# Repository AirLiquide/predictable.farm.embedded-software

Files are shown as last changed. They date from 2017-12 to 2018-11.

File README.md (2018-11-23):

Predictable Farm — Embedded software
---

### Introduction

Two versions are available :

  - a legacy version for the **Arduino Yùn** (_it was the first platform used for the predictable.farm project_)
  - An up-to-date version for the **Siemens IOT2000** boards

### Licenses

Our work is licensed under the MIT license. See license.txt.

**This work uses sofware that is licensed under CC BY-NC-SA 3.0, GNU LGPL, and BSD licenses. The respective files have kept their original license notices.**

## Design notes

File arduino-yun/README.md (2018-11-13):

Predictable Farm — Embedded software — Yùn Bridge Flavour
---

### Introduction

This folder contains the code for the Yùn version, including :

  - `arduino-IO-node` : the code for the ATmega32u4 microcontroller;
  - `linino` : the code for the Linino Linux distribution running on the Atheros chipset.

See the relevant README in each folder for more information.

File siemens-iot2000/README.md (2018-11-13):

Predictable Farm — Embedded software — Siemens iot2000 flavour
---

### Introduction

This is the on-board software for the predictable farm devices.
It is self-updateable via [SWUpdate](https://github.com/sbabic/swupdate).

**Configuration**

The zone pattern indicate the naming pattern for the farms, e.g. `http://farm1.my.domain`, `http://farm2.my.domain`, if necessary. Else, the default server url is used.

Devices are supposed to be hostnamed as per the following pattern : `predictable{XXX}.local` where `{XXX}` is an integer.

### Installation

Dependencies : **mraa** and **socket.io**

> This software is to be installed on the device; hence, having limited resources, we favor a general installation of dependencies, not using `npm`.
> As such, node modules should be installed in `/usr/lib/node_modules/` beforehand; We do not provide a `package.json` file for this repo (but it would be trivial to do so if you need it).

The `start.sh`  script should be launched at boot time.

The `local-engine.js` file is the compiled bundle from the [Predictable farm offline strategy generator](http://airliquide.github.com/predictable.farm.embedded-software.offline-strategy-generator). If the latter is updated, compile it for `iot2000` and put it in the root folder of your installation.

### To start everything

    cd predictable-farm
    forever start forever.json

### To stop all services 

    forever stopall

### To operate on a single script

    forever restart <script>

### Relevant documentation

  - [Intel IOT MRAA lib](http://iotdk.intel.com/docs/master/mraa/node/classes/i2c.html#method_readWordReg)
  - [MRAA Galileo Gen 2 limitations](https://github.com/intel-iot-devkit/mraa/blob/master/docs/galileorevh.md)
  - [Galileo Gen 2 Pin mapping](https://link.springer.com/chapter/10.1007/978-1-4302-6838-3_14)
  - [Quark X1000 i2C documentation](https://github.com/slavaim/Linux-Intel-Galileo-Gen2-QuarkX1000/tree/master/BSPv1.1.0/linux_v3.8.7/work/Documentation/i2c)

### To enable / disable the i2c bus power

    mraa-gpio set 04 00 # Disable
    mraa-gpio set 04 01 # Enable

### To force-stop the i2c bus

    # Force deactivate PIN gpio6 (IO4) - Bus I2C
    echo 0 > /sys/class/gpio/gpio6/value

### To create a new release / update the code

We use SWupdate (https://github.com/sbabic/swupdate) with its Yocto layer : https://github.com/sbabic/meta-swupdate/tree/morty.

    ./create_release.sh

This will create a `predictable-farm_<version>.swu` file in the root folder, that can be used with swupdate on the target device :

    swupdate_unstripped --hwrevision iot2040:rev1 -i predictable-farm_<version>.swu

> release_install.sh and release_restart.sh are pre and post install scripts used by swupdate during the update process.

### CAD Files

In order to build the necessary interface board, the CAD folder includes : the Fritzing source design + the BOM and relevant datasheets.

### License

MIT. See License.txt file

**This work uses sofware that is licensed under GPL-2.0. The respective files have kept their original license notices.**

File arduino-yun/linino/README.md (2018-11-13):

Predictable Farm — Embedded software — Yùn Bridge Flavour
---

Needs NodeJS 0.10.* and BusyBox.

### Installation

Dependencies : **serialport** and **socket.io-client**

> This software is to be installed on the device; hence, having limited resources, we favor a general installation of dependencies, not using `npm`.
> As such, node modules should be installed in `/usr/lib/node_modules/` beforehand; We do not provide a `package.json` file for this repo (but it would be trivial to do so if you need it).

#### ID bootstrapping

To include the correct id, you must run the `scripts/bootstrap.sh` script first, with the correct ID in the **valueID** file.

#### How to install the bridge service

Node modules should be installed in `/usr/lib/node_modules/` beforehand; NPM is not a valid choice to install dependencies on this system.

copy `bridge.service` to `/etc/init.d/bridge` and make it executable :

    cp /root/bridge.service /etc/init.d/bridge
    chmod +x /etc/init.d/bridge

Enable it for auto starting at boot :

    /etc/init.d/bridge enable

#### Swap

It's better to have some swap to manage RAM overflows :

    cd /
    mkdir swap
    dd if=/dev/zero of=/swap/yunswapfile bs=1M count=512
    # wait a bit here, takes ~10min
    mkswap /swap/yunswapfile
    swapon /swap/yunswapfile
    uci add fstab swap
    uci set fstab.@swap[0].device=/swap/yunswapfile
    uci set fstab.@swap[0].enabled=1
    uci set fstab.@swap[0].fstype=swap
    uci set fstab.@swap[0].options=default
    uci set fstab.@swap[0].enabled_fsck=0
    uci commit # might trigger some errors, but that's ok
    reboot

#### Crontab

Make the reboot script executable if necessary :

    chmod +x /root/scripts/safeRebootAtMidnight.sh

And create a **crontab** for root :

    5 0 * * * /root/scripts/safeRebootAtMidnight.sh

#### Update code

Use the update script :

    /scripts/update.sh

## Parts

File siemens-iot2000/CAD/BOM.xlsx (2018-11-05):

Repère | Qté | Ref. Fabricant | Description | Fabricant | Fournisseur | Ref. Fournisseur | Prix unitaire | Prix total
J1 | 1 | EM366002 | Terminal bornier 2P 5mm | Bussman | Mouser | 504-EM366002 | 0.47 € | 0.47 €
J2 | 1 | S3B-PH-K-S (LF)(SN) | Connecteur 3 pin JST PH | JST | Digikey (ou RS) | 455-1720-ND | 0.15 | 0.15 €
J101, J102, 103, J104, 105, 106 | 6 | 110990030 | Connecteurs Grove | Seeed Studio | Mouser | 713-110990030 | 1.23 € | 1.23 €
U1 | 1 | 95503-2881 | Connecteur Ethernet RJ45 | Molex | Mouser | 538-95503-2881 | 0.69 € | 0.69 €
IC1, IC2 | 2 | FDS8958A-F085 | Dual N & P-Channel PowerTrench | Fairchild | Mouser | 512-FDS8958A | 0.76 € | 1.53 €
IC3 | 1 | TSR2-2450 | Convertisseur DC/DC | Traco | Mouser | 495-TSR2-2450 | 11.21 € | 11.21 €
D2,D3 | 2 | SMAJ60A-TP | Suppresseur ESD / diodes | MCC | Mouser | 833-SMAJ60A-TP | 0.51 € | 1.02 €
R7, R9 | 2 | MBB02070C1004FCT00 | 1 M 5% | Vishay | Mouser | 594-MBB02070C1004FCT | 0.08 € | 0.16 €
R8, R10 | 2 | MBB02070C4703FCT00 | 470k 1% | Vishay | Mouser | 594-MBB02070C4703FCT | 0.09 € | 0.19 €
R3, R4, R11, R12 | 4 | MBB02070C1002FCT00 | 10k 1% | Vishay | Mouser | 594-MBB02070C1002FCT | 0.09 € | 0.38 €
C1, C3 | 2 | K101J15C0GH53H5H | 100V, 0.1 nF (100pf) | Vishay | Mouser | 594-K101J15C0GH53H5H | 0.21 € | 0.43 €
C2, C4 | 2 | C315C102J3H5TA91707301 | 25V 1 nF | Kemet | Mouser | 80-C315C102J3H9170TR | 0.63 € | 1.26 €
C5 | 1 | C315C103M5U5TA | 50V 0.01µF | Kemet | Mouser | 80-C315C103M5U | 0.25 € | 0.25 €
Headers 20P - to break away | 2 | 22-28-4205 | Header breakaway 20P 1R | Molex | Mouser | 538-22-28-4205 | 0.92 € | 1.84 €
IC5 | 1 | TCA9517 | Level-Shifting I2C Bus Repeater | TI | Mouser | 595-TCA9517DR | 0.80 € | 0.80 €
 |  |  |  |  |  |  | Mouser | 21.44 €
 |  |  |  |  |  |  | Digikey | 0.15 €
 |  |  |  |  |  |  | Total | 21.59 €

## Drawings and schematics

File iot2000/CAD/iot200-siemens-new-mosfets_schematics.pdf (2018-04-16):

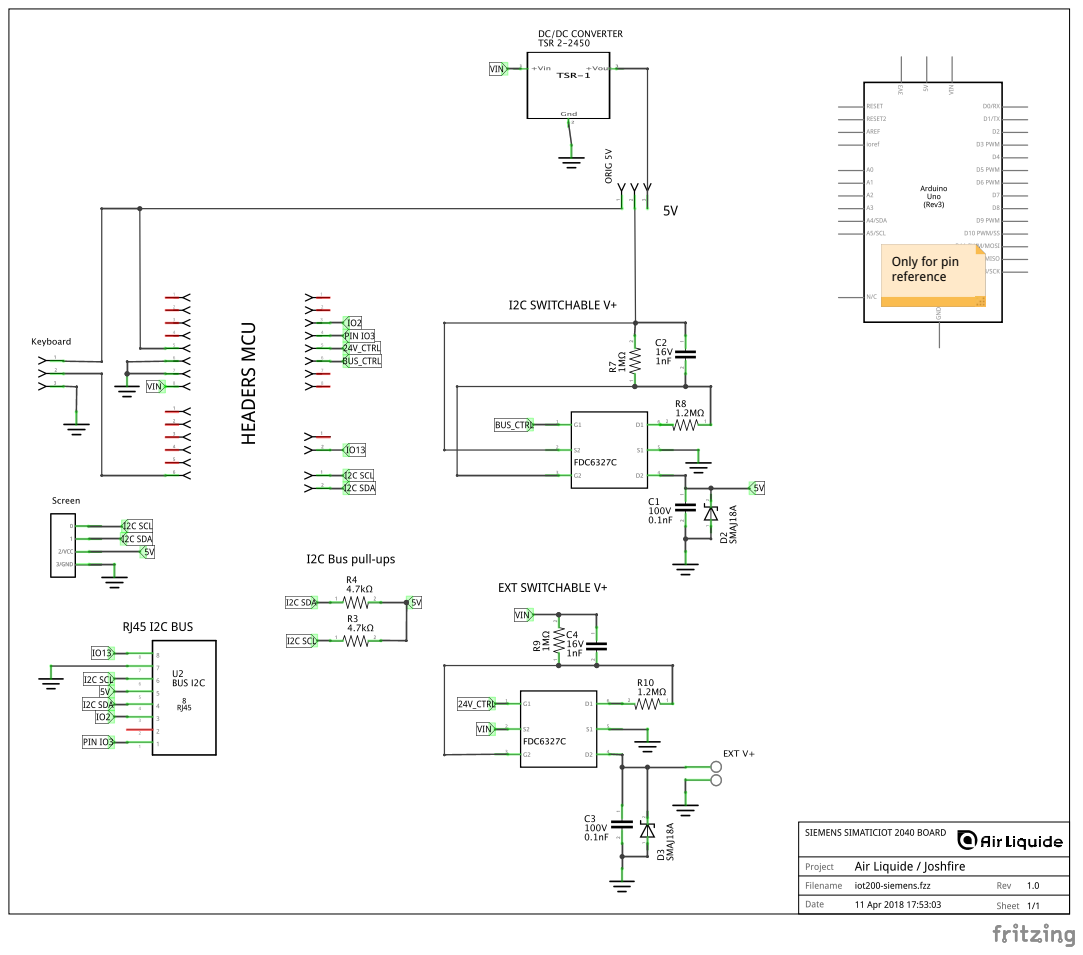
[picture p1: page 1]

Only for pin
reference

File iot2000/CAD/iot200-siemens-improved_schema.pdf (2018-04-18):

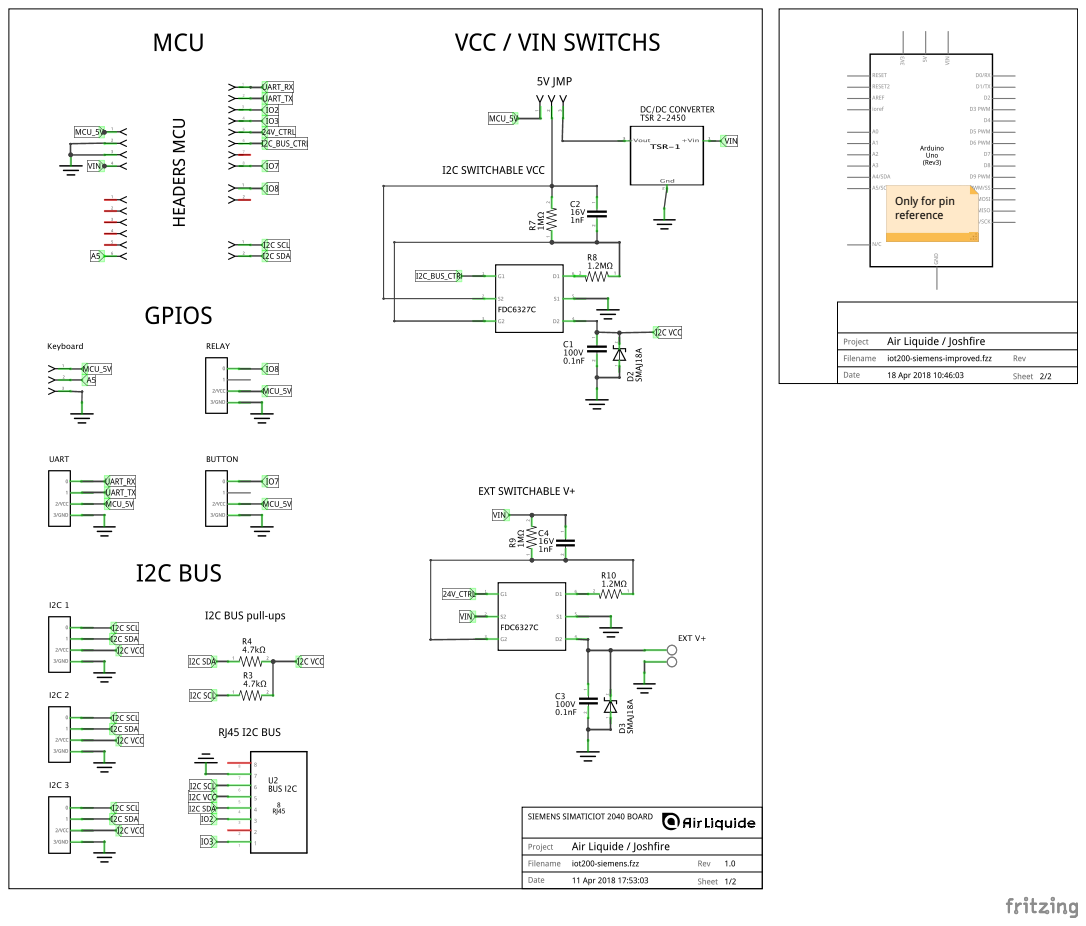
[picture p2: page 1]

Only for pin
reference

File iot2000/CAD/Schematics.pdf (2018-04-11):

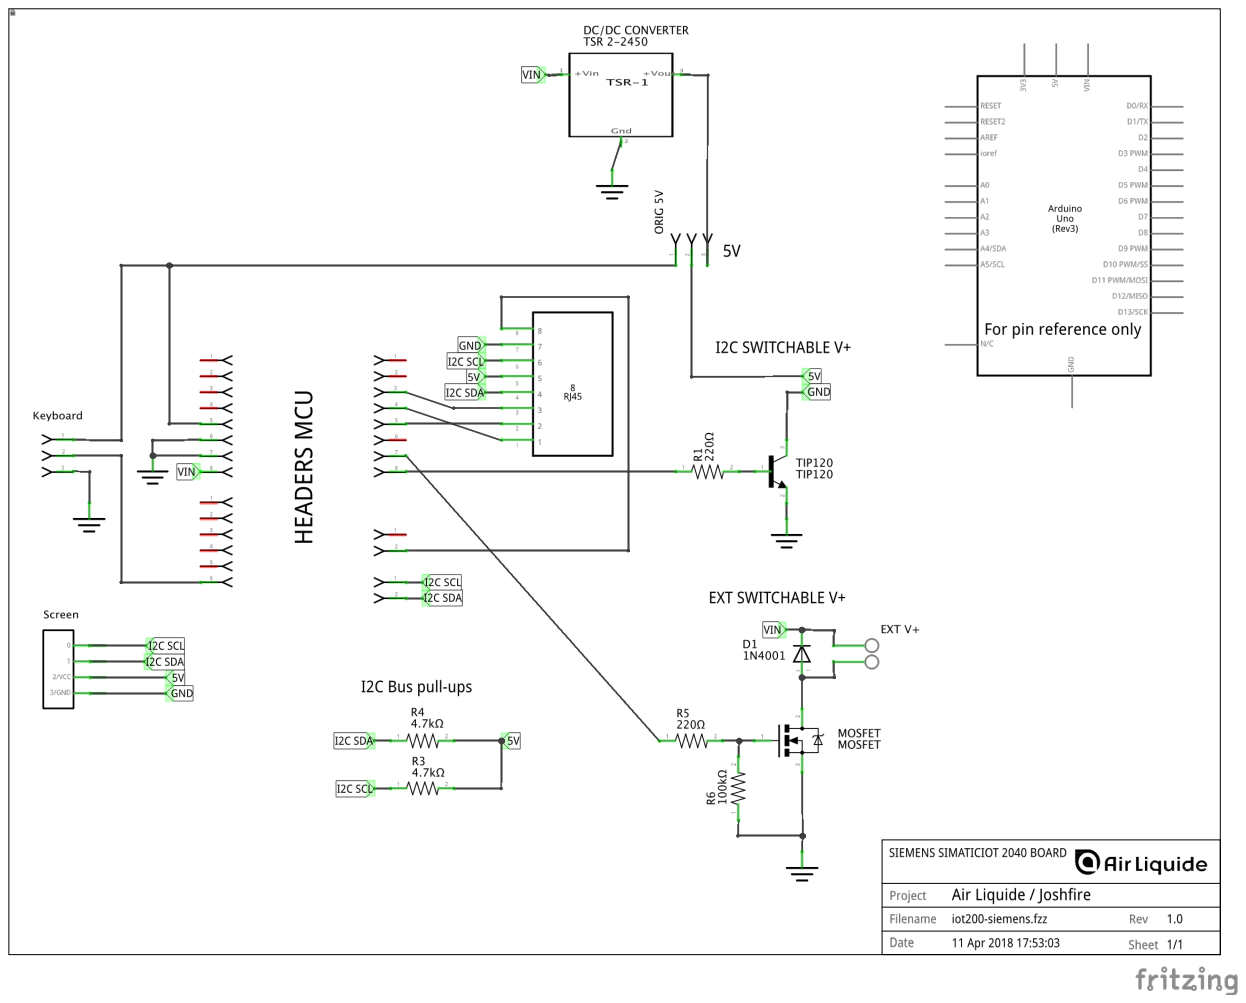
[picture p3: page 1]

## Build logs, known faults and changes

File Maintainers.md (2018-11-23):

Sébastien LALAURETTE <sebastien.lalaurette@airliquide.com>

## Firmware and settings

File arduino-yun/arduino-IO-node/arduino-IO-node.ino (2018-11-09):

/*
  Copyright (C) Air Liquide S.A,  2017
  Author: Sébastien Lalaurette and Gwennaëlle Remy, La Factory, Creative Foundry
  This file is part of Predictable Farm project.

  The MIT License (MIT)

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
  See the LICENSE.txt file in this repository for more information.
*/
#include "config.h"
#include "Relay.h"
#include "YunBridge.h"
#include "SensorTypes.h"
#include "Sensors.h"
#include "LCD.h"
#include "Menu.h"
#include "Button.h"

#if defined(ARDUINO) && ARDUINO >= 100
#include "Arduino.h"
#else
#include "WProgram.h"
#endif

#define CALL_COMPENSATION_EC 15
#define CALL_COMPENSATION_RTD 11 //at least 3 less than CALL_COMPENSATION_EC
#define CALL_WATER_SENSOR 7//at least 3 less than CALL_COMPENSATION_RTD
#define VALUE_SENSOR_SEND_LINUX 0
#define NBRE_CYCLE 20 //can't be less than CALL_COMPENSATION_EC

#define TIME_CYCLE_MS 150

#define LCD_DISPLAY


/* Global Variables */
//unsigned char deviceConnected = 0 ;
long previousMillis = 0;
long elapsed = 0;
uint8_t menu = 0;
unsigned char bridgeCommandType = 0;
int bridgeCommandValue = 0;
#ifdef LCD_DISPLAY
LCD myLCD;
#endif

YunBridge bridge;
Relay relay;
Sensors mySensors;
#ifdef USE_MENU
Menu myMenu;
#endif



#ifdef USE_DASHBOARD_VIEW
Button myButton;
#endif

void setup()
{

  Serial.begin(9600);


#ifdef DEBUG
  while (!Serial) {
    ; // wait for serial port to connect. Needed for native USB port only
  }
#endif


#ifndef I2CLIB
  Wire.begin();
  //Wire.setClock(10000);
#else
  I2c.reset();
  I2c.begin();
  I2c.timeOut(80);
  I2c.setSpeed(0);
#endif


  // initialize classes
  bridge.init();

  myLCD.WorkingModeConf(OFF, ON, WM_CharMode);
  //8*16 font size, auto new line, black character on white back ground.
  myLCD.FontModeConf(Font_6x8, FM_ANL_AAA, BLACK_BAC);

  //myLCD.Init();

  relay.init(&myLCD, &bridge);
  mySensors.init(&myLCD, &bridge);

#ifdef LCD_DISPLAY
  //Clean the screen with black or white.
  myLCD.CleanAll(WHITE);    //Clean the screen with black or white.
#endif
#ifdef USE_MENU
  myMenu.init(&myLCD, &mySensors, &relay);
  menu = myMenu.getCurrentMenuIndex();
#endif


#ifdef USE_DASHBOARD_VIEW
  // need to init button here as we don't use the menu capability
  myButton = Button();

  //delimiter for date

  myLCD.DrawHLineAt(0, LCD_X_SIZE_MAX - 1, ROW_OFFSET - 2, WHITE);
  //delimiter for time
  //myLCD.DrawVLineAt(0, ROW_OFFSET -2, (CHAR_OFFSET*15)-2, WHITE);
  //delimiter for status bits
  myLCD.DrawHLineAt(0, LCD_X_SIZE_MAX - 1, (5 * ROW_OFFSET) - 3, WHITE);
  for (int i =1; i<7; i++)  myLCD.DrawVLineAt((5 * ROW_OFFSET) - 3, LCD_Y_SIZE_MAX - 1, (i * 2* CHAR_OFFSET) - 4, WHITE);
  // delimiter for device ID bottom right corner
  myLCD.DrawVLineAt((5 * ROW_OFFSET) - 3, LCD_Y_SIZE_MAX - 1, (15 * CHAR_OFFSET) - 2, WHITE);
  //inside symbol
  myLCD.DrawRectangleAt(0, 2 * ROW_OFFSET , 11, 7, WHITE_NO_FILL);
  myLCD.DrawCircleAt(5, 2 * ROW_OFFSET + 3 , 2, WHITE_FILL);

  //outside symbol
  myLCD.DrawCircleAt(5, 3 * ROW_OFFSET + 3 , 2, WHITE_FILL);
  //notification area
  myLCD.DrawHLineAt(0, LCD_X_SIZE_MAX - 1, (2 * ROW_OFFSET) - 3, WHITE);


  /*   myLCD.DispStringAt("12:23",CHAR_OFFSET*15,0);
     //myLCD.DispStringAt("Custom",0,ROW_OFFSET);
     myLCD.DispStringAt("SAM 25 JUL",0,0);
     myLCD.DispStringAt("RDV DENTISTE 16H15",0,(4* ROW_OFFSET));*/
#endif

#ifdef DEBUG
  Serial.println("ready");
#endif

}

void send_relay_state()
{
  if (relay.on) {
   bridge.sendInteger("relay1", relay.getState(0) | (relay.getMode(0) << 1));
   bridge.sendInteger("relay2", relay.getState(1) | (relay.getMode(1) << 1));
   bridge.sendInteger("relay3", relay.getState(2) | (relay.getMode(2) << 1));
   bridge.sendInteger("relay4", relay.getState(3) | (relay.getMode(3) << 1));
  }
}

uint8_t updateCounter = CALL_WATER_SENSOR;
void loop()
{
  char buf[21];
  memset(buf, 0, 21);
#ifdef DEBUG
  Serial.print(".");
#endif
  previousMillis = millis();

#ifdef I2CLIB
  I2c.begin();
#endif

#ifdef USE_DASHBOARD_VIEW

  uint8_t symbol = 32; //space
            
  // get btn state if any
  char btnId[4];
  btnId[0] = 'b';
  btnId[1] = 't';
  btnId[2] = 'n';
  unsigned char btnCurr = myButton.getCurrent();
  unsigned char btnPrev = myButton.getPrev(btnCurr);
  if (btnCurr && btnPrev != btnCurr)
  {
    btnId[3] = (btnCurr + 48);
    bridge.sendInteger(btnId, 1);//send btn down
    // myLCD.DispStringAt(btnId,0, 5 * ROW_OFFSET);
  }
  if (btnPrev && btnPrev != btnCurr) // send state to yun
  {
    btnId[3] = (btnPrev + 48);
    bridge.sendInteger(btnId, 0); //send btn release
    // myLCD.DispStringAt(btnId,40, 5 * ROW_OFFSET);
  }
#endif /*USE_DASHBOARD_VIEW*/

  /********************************************/
  /* update sensors values                    */
  /********************************************/

  if (updateCounter == CALL_COMPENSATION_EC)
  {
    mySensors.compensationEC();//We compensate the sensors if we have a EC probe
  }
  else if (updateCounter == CALL_COMPENSATION_RTD)
  {
    mySensors.compensationTemp();//We compensate the sensors if we have a temperature probe
  }
  else if (updateCounter == CALL_WATER_SENSOR)
  {
    mySensors.waterCall();// We call the water sensors
  }
  if (updateCounter == VALUE_SENSOR_SEND_LINUX) {
#ifdef USE_MENU
    mySensors.update(true, true, menu);
#endif

#ifdef USE_DASHBOARD_VIEW
    // update sensor and store value in variables
    mySensors.update(false, true, 0);


#ifdef LCD_DISPLAY
    // update screen content
    myLCD.DispStringAt("               ", CHAR_OFFSET * 3, 2 * ROW_OFFSET);
    myLCD.CharGotoXY(CHAR_OFFSET * 3, 2 * ROW_OFFSET);
#if 1
    float temp = 19.43;
    if (temp > -10) myLCD.CharGotoXY(CHAR_OFFSET * 4, 2 * ROW_OFFSET);
    else myLCD.CharGotoXY(CHAR_OFFSET * 3, 2 * ROW_OFFSET);
    myLCD.print(temp, 0);
    myLCD.DrawCircleAt((CHAR_OFFSET * 6) + 2, 2 * ROW_OFFSET, 1, WHITE_NO_FILL); //degree symbol
    myLCD.DispStringAt("C ", CHAR_OFFSET * 7, 2 * ROW_OFFSET);
    //Relative humidtity
    myLCD.print(32.87, 0);
    myLCD.print("% ");
    //goutte d'eau : disc + point
    myLCD.DrawCircleAt((CHAR_OFFSET * 12) + 2, 2 * ROW_OFFSET + 4, 2, WHITE_FILL);
    myLCD.DrawDotAt((CHAR_OFFSET * 12) + 2, 2 * ROW_OFFSET + 1, WHITE);
    //co2
    myLCD.CharGotoXY(CHAR_OFFSET * 14, 2 * ROW_OFFSET);
    myLCD.print(1192);
    myLCD.print("ppm");
#endif
#ifdef SENSOR_TYPE_AIR_TEMPERATURE_SENSOR
    myLCD.print(mySensors.air_temperature, 0);
    myLCD.print("\'C ");
#endif
#ifdef SENSOR_TYPE_RELATIVE_HUMIDITY_SENSOR
    myLCD.print(mySensors.air_humidity, 0);
    myLCD.print("% ");
#endif /*SENSOR_TYPE_RELATIVE_HUMIDITY_SENSOR*/
#ifdef SENSOR_TYPE_CO2_SENSOR
    myLCD.print(mySensors.air_CO2);
    myLCD.print("ppm");
#endif /*SENSOR_TYPE_CO2_SENSOR*/
#endif /* LCD_DISPLAY*/
#endif /* USE_DASHBOARD_VIEW*/;

    /*****************************************************/
    /* send commands, status or values to the Linux side */
    /*****************************************************/


    while (bridge.getCommand(&bridgeCommandType, &bridgeCommandValue, buf) > 0)
    {
      uint8_t num = bridgeCommandType - BRIDGE_RELAY_1;
      switch (bridgeCommandType)
      {
        case BRIDGE_RELAY_1:
        case BRIDGE_RELAY_2:
        case BRIDGE_RELAY_3:
        case BRIDGE_RELAY_4:
          if (bridge.socketReady) {
#ifdef DEBUG
            Serial.print(F("R"));
            Serial.print(num);
            Serial.print(F(":"));
            Serial.println(bridgeCommandValue);
#endif
            if (bridgeCommandValue >= RELAY_OFF && bridgeCommandValue <= RELAY_FORCED_ON ) { // make sure we dont get garbage from linux during boot or eventual linux side app crash
              if ((bridgeCommandValue & 0x1) == RELAY_ON) relay.setState(0, num);
              else relay.setState(1, num);
              if ((bridgeCommandValue & 0x2)  == RELAY_MODE_AUTO) relay.setMode(RELAY_MODE_AUTO, num);
              else relay.setMode(RELAY_MODE_MANUAL, num);
              relay.popup(num);
            }
          }
          break;
        case BRIDGE_OS:
          bridge.linuxReady = (bridgeCommandValue == BRIDGE_OS_UP);
#ifdef USE_MENU
          if (myMenu.getCurrentMenuIndex() == n_menu_main) // update id displayed on main menu
            myMenu.mainMenu();
#endif
          break;
        case BRIDGE_DEVICE:
          bridge.deviceID = bridgeCommandValue;
#ifdef USE_MENU
          if (myMenu.getCurrentMenuIndex() == n_menu_main) // update id displayed on main menu
            myMenu.mainMenu();
#endif

#ifdef USE_DASHBOARD_VIEW
          myLCD.DispStringAt("ID:", 15 * CHAR_OFFSET, 5 * ROW_OFFSET);
          myLCD.print(bridge.deviceID);
#endif
          break;

#ifdef USE_DASHBOARD_VIEW
        case BRIDGE_SYSTEM_TIME:
          myLCD.DispStringAt("                     ", 0, 0);
          myLCD.DispStringAt(buf, 0, 0);

          Serial.print("time:");
          Serial.println(buf);
          break;
        /*  case BRIDGE_SYSTEM_DATE:
             myLCD.DispStringAt(buf,0,0);
             break;*/
        case BRIDGE_SYSTEM_NOTIF:
          myLCD.DispStringAt("                     ", 0, 1 * ROW_OFFSET);
          myLCD.DispStringAt(buf, 0, 1 * ROW_OFFSET);
          break;
        case BRIDGE_STATE_SCENARIO:
            myLCD.CharGotoXY(13 * CHAR_OFFSET , 5 * ROW_OFFSET);
            if (bridgeCommandValue) 
            {
              symbol = 83;
            }
          break;
        case BRIDGE_STATE_WINDOW:
            myLCD.CharGotoXY(10 * CHAR_OFFSET , 5 * ROW_OFFSET);
            if (bridgeCommandValue) 
            {
              symbol = 70;
            }
          break;
        case BRIDGE_STATE_UP:
            myLCD.CharGotoXY(0 * CHAR_OFFSET , 5 * ROW_OFFSET);
            if (bridgeCommandValue) 
            {
              symbol = ArrowUp;
            }
            myLCD.write(symbol);
          break;
        case BRIDGE_STATE_DOWN:
            myLCD.CharGotoXY(2 * CHAR_OFFSET , 5 * ROW_OFFSET);
            if (bridgeCommandValue) 
            {
              symbol = ArrowDown;
            }
            myLCD.write(symbol);
          break;
        case BRIDGE_STATE_LIGHT:
            myLCD.CharGotoXY(4 * CHAR_OFFSET , 5 * ROW_OFFSET);
            if (bridgeCommandValue) 
            {
              symbol = 76;
            }
            myLCD.write(symbol);
          break;
        case BRIDGE_STATE_CLIMATE:
            myLCD.CharGotoXY(6 * CHAR_OFFSET , 5 * ROW_OFFSET);
            if (bridgeCommandValue) 
            {
              symbol = 67;
            }
            myLCD.write(symbol);
            break;
        case BRIDGE_SYSTEM_REMOTE_INFO:
          myLCD.DispStringAt("                     ", 0, 4 * ROW_OFFSET);
          myLCD.DispStringAt(buf, 0, 4 * ROW_OFFSET);
          break;
        case BRIDGE_WEATHER_FORECAST:
          myLCD.DispStringAt("                     ", 0, 3 * ROW_OFFSET);
          myLCD.DispStringAt(buf, 0, 3 * ROW_OFFSET);
          break;
#endif  /*USE_DASHBOARD_VIEW*/
        case BRIDGE_SYSTEM_CONFIG:
        case BRIDGE_SYSTEM_REBOOT:
        case BRIDGE_SYSTEM_UPDATE:
          /*  if (bridgeCommandValue == 67) {
              myLCD.CleanAll(WHITE);
              myLCD.CharGotoXY(2 * CHAR_OFFSET, 2 * ROW_OFFSET);
              myLCD.print(F("Updating"));

              //Serial.print(F("U "));
              delay(10000);
              //myLCD.print("Reset");
            }*/
          break;
        case BRIDGE_NETWORK:
          bridge.networkReady = bridge.linuxReady && (bridgeCommandValue > BRIDGE_NETWORK_UP);
          bridge.socketReady = bridge.linuxReady && (bridgeCommandValue == BRIDGE_NETWORK_SOCKET);
#ifdef USE_MENU
          if (myMenu.getCurrentMenuIndex() == n_menu_main) // update network status
            myMenu.mainMenu();
#endif
#ifdef USE_DASHBOARD_VIEW
            myLCD.CharGotoXY(8 * CHAR_OFFSET , 5 * ROW_OFFSET);
            if (bridgeCommandValue > BRIDGE_NETWORK_UP) 
            {
              if(bridgeCommandValue == BRIDGE_NETWORK_SOCKET) symbol = 64;
              else symbol = 35;
            }
            myLCD.write(symbol);
#endif  /*USE_DASHBOARD_VIEW*/

          break;
        default:

#ifdef DEBUG
          Serial.print(F("D "));
          Serial.println(bridgeCommandType);
#endif
          break;

      }
      memset(buf, 0, 21);
    }

    //send relay state to Linux
    send_relay_state();
    


    updateCounter = NBRE_CYCLE;
  }
  else
    updateCounter --;



  /********************************************/
  /* Update relay values                      */
  /********************************************/
  relay.updateState();

#ifdef LCD_DISPLAY

#ifdef USE_MENU
  /*****************************************************/
  /*  MENU DISPLAY                                     */
  /*****************************************************/
  menu = myMenu.printMenu(menu);
#endif /*USE MENU*/
#endif /* LCD_DISPLAY */
#ifdef I2CLIB
  I2c.end();
#endif

  elapsed = (millis() - previousMillis);
  if (elapsed < TIME_CYCLE_MS) delay(TIME_CYCLE_MS -  elapsed); //loop every 150 msec exactly

}

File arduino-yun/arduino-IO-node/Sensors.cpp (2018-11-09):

/*
  Copyright (C) Air Liquide S.A,  2017
  Author: Sébastien Lalaurette and Gwennaëlle Remy, La Factory, Creative Foundry
  This file is part of Predictable Farm project.

  The MIT License (MIT)

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
  See the LICENSE.txt file in this repository for more information.
*/
#include "Sensors.h"
 
#ifdef SENSOR_TYPE_EZO_SENSOR
EZO myEZO;
#endif

enum _sensor_item {
  _item_rtd = 1,
  _item_ph ,
  _item_ec,
  _item_do,
  _item_orp,
  _item_water_level,
 /* _item_light_PAR,
  _item_light_UV ,
  _item_air_temperature,
  _item_air_pressure,
  _item_air_relative_humidity,
  _item_air_CO,
  _item_air_CO2,*/
  _item_soil_temperature,
  _item_soil_moisture,
  _item_last
};


/**
   \fn void Sensors::init(LCD * p_LCD,  YunBridge * p_bridge)
   \brief initialize Sensors.cpp detect sensors connected, by scaning th i2c bus, then initialize them

   \param pointers to LCD.cpp, YunBridge.cpp
   \return n/a
*/
void Sensors::init(LCD * p_LCD,  YunBridge * p_bridge)
{

  p_myLCD = p_LCD;
  p_myBridge = p_bridge;
  
#ifdef SENSOR_TYPE_EZO_SENSOR
  myEZO = EZO();
#endif
  //initialize values tamp

#ifdef SENSOR_TYPE_LOW_COST_SUNLIGHT_SENSOR
  sensor_light_lux = 0;

  sensor_light_uv  = 0;
#endif
  delay(2000);
  // detect I2C sensors
  detect();

}

/**
   \fn void  Sensors::detect()
   \brief test which sensors are connected and initialize thel

   \param n/a
   \return n/a
*/
void  Sensors::detect()
{
  on = false;
  
#ifdef SENSOR_TYPE_WATER_TEMPERATURE_SENSOR
  water_temperature = -1023;
#endif

#ifdef SENSOR_TYPE_PAR_SENSOR
  sensor_light_par = 0;
#endif


#ifdef SENSOR_TYPE_UV_SENSOR
  sensor_light_uv = 0;
#endif

#ifdef SENSOR_TYPE_AIR_TEMPERATURE_SENSOR
  sensor_air_temperature = 0;
#endif

#ifdef SENSOR_TYPE_PRESSURE_SENSOR
  sensor_air_pressure = 0;
#endif

#ifdef SENSOR_TYPE_RELATIVE_HUMIDITY_SENSOR
  sensor_air_relative_humidity = 0;
#endif


#ifdef SENSOR_TYPE_CO_SENSOR
  sensor_air_CO = 0;
#endif

#ifdef SENSOR_TYPE_CO2_SENSOR
  sensor_air_CO2 = 0;
#endif

#ifdef SENSOR_TYPE_SOIL_TEMPERATURE_SENSOR
  sensor_soil_temperature = 0;
#endif

#ifdef SENSOR_TYPE_SOIL_MOISTURE_SENSOR
  sensor_soil_moisture = 0;
#endif

#ifdef SENSOR_TYPE_WATER_TEMPERATURE_SENSOR
  sensor_water_temperature = 0;
#endif


#ifdef SENSOR_TYPE_WATER_PH_SENSOR
  sensor_water_ph = 0;
#endif

#ifdef SENSOR_TYPE_WATER_EC_SENSOR
  sensor_water_ec = 0;
#endif

#ifdef SENSOR_TYPE_WATER_DO_SENSOR
  sensor_water_do = 0;
#endif

#ifdef SENSOR_TYPE_WATER_ORP_SENSOR
  sensor_water_orp = 0;
#endif  

#ifdef SENSOR_TYPE_WATER_LEVEL_SENSOR
  sensor_water_level = 0;
#endif

  sensor_item = _item_rtd;

  uint8_t error, address;
  //uint8_t nDevices = 0;
  float essay;

  p_myLCD->CleanAll(WHITE);
  lcdLine = 0;

#ifdef DEBUG
  Serial.println("Scan I2C");
#endif


  for (address = 1; address < 127; address++ )
  {
    // The i2c_scanner uses the return value of
    // the Write.endTransmisstion to see if
    // a device did acknowledge to the address.
#ifndef I2CLIB
    Wire.beginTransmission(address);
    error = Wire.endTransmission();
#else
  I2c.start();
  error = I2c.sendAddress(SLA_W(address));
  I2c.stop();
#endif
    if (error == 0)
    {
#ifdef DEBUG
      Serial.print(F("I2C 0x"));
      if (address < 16)
        Serial.print("0");
      Serial.print(address, HEX);
      Serial.print(" : ");
      Serial.println(address);
#endif

      switch (address) {

#ifdef SENSOR_TYPE_WATER_LEVEL_SENSOR
        case WATER_LEVEL_ADDR:
          on = true;
          myWaterlevel = Waterlevel();

          p_myLCD->DispStringAt(WATER_LEVEL_DNAME, 0, lcdLine * ROW_OFFSET);
          printOk();

          sensor_water_level = 1;
          break;

#endif
#ifdef SENSOR_TYPE_PRESSURE_SENSOR
        ///BAROMETER + TEMP
        case AIR_PRESSURE_MEASUREMENT_ADDR:
          on = true;
          myBarometer = Barometer();
          myBarometer.begin();

          p_myLCD->DispStringAt(AIR_PRESSURE_MEASUREMENT_DNAME, 0, lcdLine * ROW_OFFSET);
          printOk();
          p_myLCD->DispStringAt(AIR_TEMPERATURE_MEASUREMENT_DNAME, 0, lcdLine * ROW_OFFSET);
          printOk();

          sensor_air_pressure = 1 ;
          break;
#endif
#ifdef SENSOR_TYPE_RELATIVE_HUMIDITY_SENSOR
        ///HUMIDITY +TEMP
        case AIR_HUMIDITY_LEVEL_MEASUREMENT_ADDR:
          on = true;
          myHum = SHTSensor(SHTSensor::SHT3X);
          //myHum.setAccuracy(SHTSensor::SHT_ACCURACY_MEDIUM);
          myHum.init();

          p_myLCD->DispStringAt(AIR_HUMIDITY_LEVEL_MEASUREMENT_DNAME, 0, lcdLine * ROW_OFFSET);
          printOk();
#ifdef SENSOR_TYPE_AIR_TEMPERATURE_SENSOR
          p_myLCD->DispStringAt(AIR_TEMPERATURE_MEASUREMENT_DNAME, 0, lcdLine * ROW_OFFSET);
          printOk();
#endif
          sensor_air_relative_humidity = 1 ;
          break;
#endif
#ifdef SENSOR_TYPE_CO2_SENSOR
        ///CO2
        case AIR_CO2_MEASUREMENT_ADDR:
          on = true;
          myi2cuart = SC16IS750(SC16IS750_PROTOCOL_I2C, SC16IS750_ADDRESS_BB);
          myCO2 = CO2();
          myCO2.init(&myi2cuart);
          myi2cuart.begin(CO2_SENSOR_BAUDRATE);
          myi2cuart.pinMode(0, INPUT);

          p_myLCD->DispStringAt(AIR_CO2_MEASUREMENT_DNAME, 0, lcdLine * ROW_OFFSET);
          printOk();

          sensor_air_CO2 = 1 ;
          break;
#endif

#ifdef SENSOR_TYPE_CO_SENSOR
        ///CO
        case AIR_CO_MEASUREMENT_ADDR:

          on = true;
          myCO = MutichannelGasSensor();
          myCO.begin();
          myCO.powerOn();

          p_myLCD->DispStringAt(AIR_CO_MEASUREMENT_DNAME, 0, lcdLine * ROW_OFFSET);
          printOk();

          sensor_air_CO = 1 ;
          break;
#endif

        ///ADC
        case ADC_MEASUREMENT_ADDR:
          on = true;
          myAdc = Adafruit_ADS1115();
#ifdef SENSOR_TYPE_SOIL_TEMPERATURE_SENSOR
          essay = myAdc.readADC_SingleEnded(2);
#ifdef DEBUG
          Serial.print("T");
          Serial.println((unsigned long)essay);
#endif
          if (essay != 0 ) {//temp , don't forget to pull down with ground line while not connected
            p_myLCD->DispStringAt(SOIL_TEMPERATURE_MEASUREMENT_DNAME, 0, lcdLine * ROW_OFFSET);
            printOk();
            soil_temperature = 0;
            sensor_soil_temperature = 1 ;
          }
#endif

#ifdef SENSOR_TYPE_PAR_SENSOR
          essay = myAdc.readADC_SingleEnded(3);
#ifdef DEBUG
          Serial.print("PAR");
          Serial.println(essay);
#endif
          if ((unsigned long)essay != 0) { //PAR, don't forget to pull down with ground line while not connected
            p_myLCD->DispStringAt(LIGHT_PAR_MEASUREMENT_DNAME, 0, lcdLine * ROW_OFFSET);
            printOk();
            sensor_light_par = 1 ; 
          //Serial.print(sensor_light_par);
          }
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

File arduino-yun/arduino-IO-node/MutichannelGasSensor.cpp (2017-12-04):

/*
    MutichannelGasSensor.cpp
    2015 Copyright (c) Seeed Technology Inc.  All right reserved.

    Author: Jacky Zhang
    2015-3-17
    http://www.seeed.cc/
    modi by Jack, 2015-8

    The MIT License (MIT)

    Copyright (c) 2015 Seeed Technology Inc.

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
    THE SOFTWARE IS PROVIDED "AS IS", WITHOUT WARRANTY OF ANY KIND, EXPRESS OR
    IMPLIED, INCLUDING BUT NOT LIMITED TO THE WARRANTIES OF MERCHANTABILITY,
    FITNESS FOR A PARTICULAR PURPOSE AND NONINFRINGEMENT. IN NO EVENT SHALL THE
    AUTHORS OR COPYRIGHT HOLDERS BE LIABLE FOR ANY CLAIM, DAMAGES OR OTHER
    LIABILITY, WHETHER IN AN ACTION OF CONTRACT, TORT OR OTHERWISE, ARISING FROM,
    OUT OF OR IN CONNECTION WITH THE SOFTWARE OR THE USE OR OTHER DEALINGS IN
    THE SOFTWARE.
*/

#include <math.h>
#include <Wire.h>
#include <Arduino.h>
#include "MutichannelGasSensor.h"

/*********************************************************************************************************
** Function name:           begin
** Descriptions:            initialize I2C
********************************************************************************************************
  void MutichannelGasSensor::begin(int address)
  {
    Serial.print("init");
    Wire.begin();

  }*/

void MutichannelGasSensor::begin()
{
  i2cAddress = DEFAULT_I2C_ADDR;
}

/*********************************************************************************************************
** Function name:           sendI2C
** Descriptions:            send one byte to I2C Wire
********************************************************************************************************
  void MutichannelGasSensor::sendI2C(unsigned char dta)
  {
  Wire.beginTransmission(i2cAddress);               // transmit to device #4
  Wire.write(dta);                                    // sends one byte
  Wire.endTransmission();                             // stop transmitting
  }*/


long MutichannelGasSensor::get_addr_dta(unsigned char addr_reg)
{
  byte test = 0;
START:
  test++;
  Wire.beginTransmission(i2cAddress);
  Wire.write(addr_reg);
  Wire.endTransmission();    // stop transmitting

  Wire.requestFrom(i2cAddress, (uint8_t)2);

  unsigned int dta = -1;

  unsigned char raw[10];
  int cnt = 0;

  while (Wire.available())
  {
    raw[cnt++] = Wire.read();
  }

  if (cnt == 0)
    if (test >1)
      goto START;
    else return dta;

  dta = raw[0];
  dta <<= 8;
  dta += raw[1];

  /*switch (addr_reg)
    {


    case CH_VALUE_CO:*/

  if (dta > 0)
  {
    adcValueR0_CO_Buf = dta;
  }
  else
  {
    dta = adcValueR0_CO_Buf;
  }

  /*  break;

    case CH_VALUE_NO2:

    if (dta > 0)
    {
      adcValueR0_NO2_Buf = dta;
    }
    else
    {
      dta = adcValueR0_NO2_Buf;
    }

    break;

    default:;
    }*/

  return dta;
}

long MutichannelGasSensor::get_addr_dta(unsigned char addr_reg, unsigned char __dta)
{
byte test=0;
START:
test++;
  Wire.beginTransmission(i2cAddress);
  Wire.write(addr_reg);
  Wire.write(__dta);
  Wire.endTransmission();    // stop transmitting

  Wire.requestFrom(i2cAddress, (uint8_t)2);

  long dta = -1;

  unsigned char raw[10];
  int cnt = 0;

  while (Wire.available())
  {
    raw[cnt++] = Wire.read();
  }

  if (cnt == 0)
    if (test >1)
      goto START;
    else return dta;

  dta = raw[0];
  dta <<= 8;
  dta += raw[1];


  return dta;
}

void MutichannelGasSensor::write_i2c(unsigned char addr, unsigned char *dta, unsigned char dta_len)
{
  Wire.beginTransmission(addr);
  for (int i = 0; i < dta_len; i++)
  {
    Wire.write(dta[i]);
  }
  Wire.endTransmission();
}


/*********************************************************************************************************
** Function name:           readData
** Descriptions:            read 4 bytes from I2C slave
********************************************************************************************************
  int16_t MutichannelGasSensor::readData(uint8_t cmd)
  {
  uint16_t timeout = 0;
  uint8_t buffer[4];
  uint8_t checksum = 0;
  int16_t rtnData = 0;

  //send command
  sendI2C(cmd);
  //wait for a while
  delay(2);
  //get response
  Wire.requestFrom(i2cAddress, (uint8_t)4);    // request 4 bytes from slave device
  while (Wire.available() == 0)
  {
    if (timeout++ > 100)
      return -2;//time out
    delay(2);
  }
  if (Wire.available() != 4)
    return -3;//rtnData length wrong
  buffer[0] = Wire.read();
  buffer[1] = Wire.read();
  buffer[2] = Wire.read();
  buffer[3] = Wire.read();
  checksum = (uint8_t)(buffer[0] + buffer[1] + buffer[2]);
  if (checksum != buffer[3])
    return -4;//checksum wrong
  rtnData = ((buffer[1] << 8) + buffer[2]);

  return rtnData;//successful
  }
*/
/*********************************************************************************************************
** Function name:           readR0
** Descriptions:            read R0 stored in slave MCU
********************************************************************************************************
  int16_t MutichannelGasSensor::readR0(void)
  {
    int16_t rtnData = 0;

    rtnData = readData(0x11);

    if(rtnData > 0)
        res0[0] = rtnData;
    else
        return rtnData;         //unsuccessful

    rtnData = readData(0x12);
    if(rtnData > 0)
        res0[1] = rtnData;
    else
        return rtnData;         //unsuccessful

    rtnData = readData(0x13);
    if(rtnData > 0)
        res0[2] = rtnData;
    else
        return rtnData;         //unsuccessful

    return 1;//successful
  }*/

/*********************************************************************************************************
** Function name:           readR
** Descriptions:            read resistance value of each channel from slave MCU
********************************************************************************************************
  int16_t MutichannelGasSensor::readR(void)
  {
    int16_t rtnData = 0;

    rtnData = readData(0x01);
    if(rtnData >= 0)
        res[0] = rtnData;
    else
        return rtnData;//unsuccessful

    rtnData = readData(0x02);
    if(rtnData >= 0)
        res[1] = rtnData;
    else
        return rtnData;//unsuccessful

    rtnData = readData(0x03);
    if(rtnData >= 0)
        res[2] = rtnData;
    else
        return rtnData;//unsuccessful

    return 0;//successful
  }*/
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

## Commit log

2017-11-28 arduino project file and main class
2017-12-07 wrong address for calibration of ORP sensor
2017-12-29 reduce occurence of relay bug by decreasing i2C speed + add delay after trigering relay
    [Relay.cpp, arduino-IO-node.ino]
2018-04-11 Fix PAR / lib ADC
2018-04-11 Add CAD files and DS
    [iot200-siemens.fzz]
2018-04-11 Add sparkling screen holes in CAD file
    [iot200-siemens.fzz]
2018-04-12 Add RJ45-Molex version
    [iot200-siemens-RJ45-Molex.fzz]
2018-04-16 Add new design with JCD6327C mosfet
    [iot200-siemens-RJ45-Molex.fzz, iot200-siemens-new-mosfets.fzz, iot200-siemens.fzz]
2018-04-18 New schema with more ports (I2C, UART, GPIO)
    [iot200-siemens-improved.fzz, iot200-siemens-new-mosfets.fzz]
2018-04-18 Add options for socket and comments
2018-04-18 Add schematics
2018-04-20 Update local-engine.js path of socket.io
2018-04-20 Change dual mosfet to 30V SO8 version
    [iot200-siemens-30V.fzz, iot200-siemens-improved.fzz]
2018-05-03 send relay state as soon as change occurs
2018-05-03 Remove some logs, fix comments
    [CO2_MHZ16_i2c.js]
2018-05-03 Fix some style issues
    [CO2_MHZ16_i2c.js]
2018-05-03 Add sensor_mode for CO2 cutoff message
2018-05-07 Add the ability to use env vars for device id and zone
2018-05-11 update from old repo + new bridge syntax + optional LCD menu or dahsboard fix using custom I2CLIB code cleanup relay code change to be less confusing and add special support for "dashboard mode " wit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
    [Barometer.cpp, LCD.cpp, LCD.h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]
2018-05-12 Dissociate Analog button state from menu + send this state to cloud
2018-05-13 weather info + send directly relay state when changed
2018-05-17 Add BOM for new version of board
    [BOM.xlsx, iot200-siemens-30V_v2.fzz]
2018-06-26 Add new flavour for TCA9517 i2c buffer
    [BOM.xlsx, iot200-siemens-30V.fzz, iot200-siemens-30V_v2.fzz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]
2018-08-09 Replace 1.2M resistor with 470k
    [BOM.xlsx, iot200-siemens-30V_vBufferTCA9517.fzz]
2018-11-05 Reset fontmode when power cycling
2018-11-05 Update with new CMS design and vertical RJ45
    [BOM.xlsx, iot200-siemens-30V_vBufferTCA9517.fzz, iot200-siemens-30V_vBufferTCA9517_vVertical.fzz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]
2018-11-09 Add License.txt to arduino-IO-node files,
    preserve actual licenses
2018-11-09 Move arduino-IO-node to arduino-yun folder
2018-11-09 Move linino files to arduino-yun folder
2018-11-09 Rename iot2000 folder
    [BOM.xlsx, iot200-siemens-30V.fzz, iot200-siemens-30V_v2.fzz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]
2018-11-09 Add license header, delete unused files
    [iot200-siemens-30V.fzz, iot200-siemens-30V_v2.fzz, iot200-siemens-30V_vBufferTCA9517.fzz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]
2018-11-13 Update CAD files
    [iot200-siemens-30V_vBufferTCA9517_vVertical_CMSDIODE.fzz]
